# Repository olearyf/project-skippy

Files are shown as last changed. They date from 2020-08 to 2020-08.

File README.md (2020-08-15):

# project-skippy
**NOTE: this project is still underway!**

A cheap DIY rocket flight computer that tracks time from launch, pressure, altitude, temperature, acceleration.

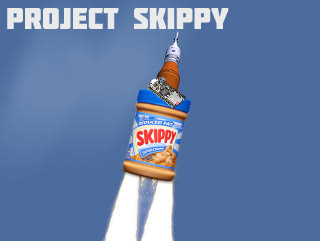
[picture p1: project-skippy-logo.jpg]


## About

While there are some neat physics tricks when it comes to approximating flight data for your model rockets, and while there are online weather apps and things to get such information such as local pressure and temperature, I thought it would be much more fun to get all this data myself. In addition to this, I can adjust the granularity to my preferences and make some sweet plots of some sweet data! Thus, Project Skippy is born; named because I started real work on the idea across from a jar of Skippy peanut butter while working in my kitchen. It's easy to use and implement, and in addition to this I supplied the 3D files for everything you need so you can print your own! All rockets use C Estes motors. 

Anyways, the idea is this: you print a rocket, make a flight computer, launch the rocket(with my super technical and complicated(jokes) remote ignition system), log the data during the flight, analyze it, and just have a good time. If that seems like something you're interested in, heres how:

## Parts List 💡
- [Adafruit Lithium Ion Polymer Battery - 3.7v 500mAh](https://www.adafruit.com/product/1578)
- [Adafruit Feather 32u4 Adalogger](https://www.adafruit.com/product/2795)
- [8 GB Micro SD Card](https://www.adafruit.com/product/1294)
- [MPL3115A2 - I2C Barometric Pressure/Altitude/Temperature Sensor](https://www.adafruit.com/product/1893)
- [Adafruit LIS3DH Triple-Axis Accelerometer](https://www.adafruit.com/product/2809)
- LED
- 220 ohm resistor (or whatever resistor you need to limit the appropriate current your LED can handle)
- some wires
- soldering iron (optional, depending on how you want to hook it up
- 3D printer (optional, you can strap this thing to any rocket your heart desires)
- M2 screws
- [small cheap camera](https://www.amazon.com/gp/product/B07X8LDZ9M/ref=ppx_yo_dt_b_asin_title_o07_s00?ie=UTF8&psc=1) (optional)

## Assembly (no BIC or TEQ 😉)
Below are some schematics made with Fritzing that detail how to wire it up. I recommend you visit the [tests](https://github.com/olearyf/project-skippy/blob/master/tests/about.md) folder and start with those, and then work your way up to the full code and full wiring below:

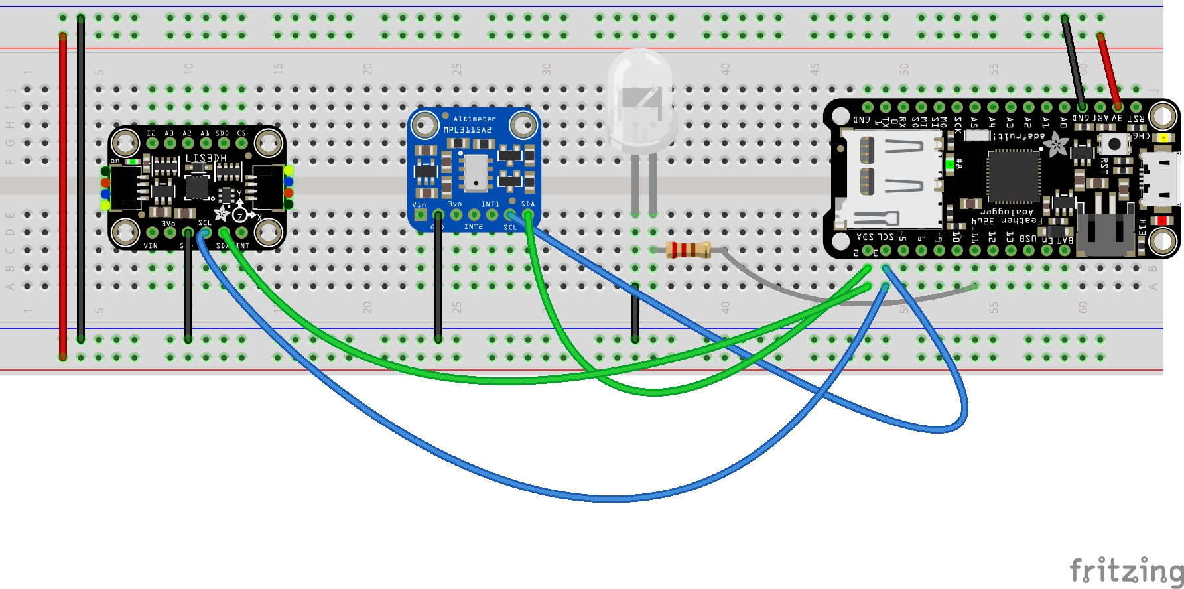
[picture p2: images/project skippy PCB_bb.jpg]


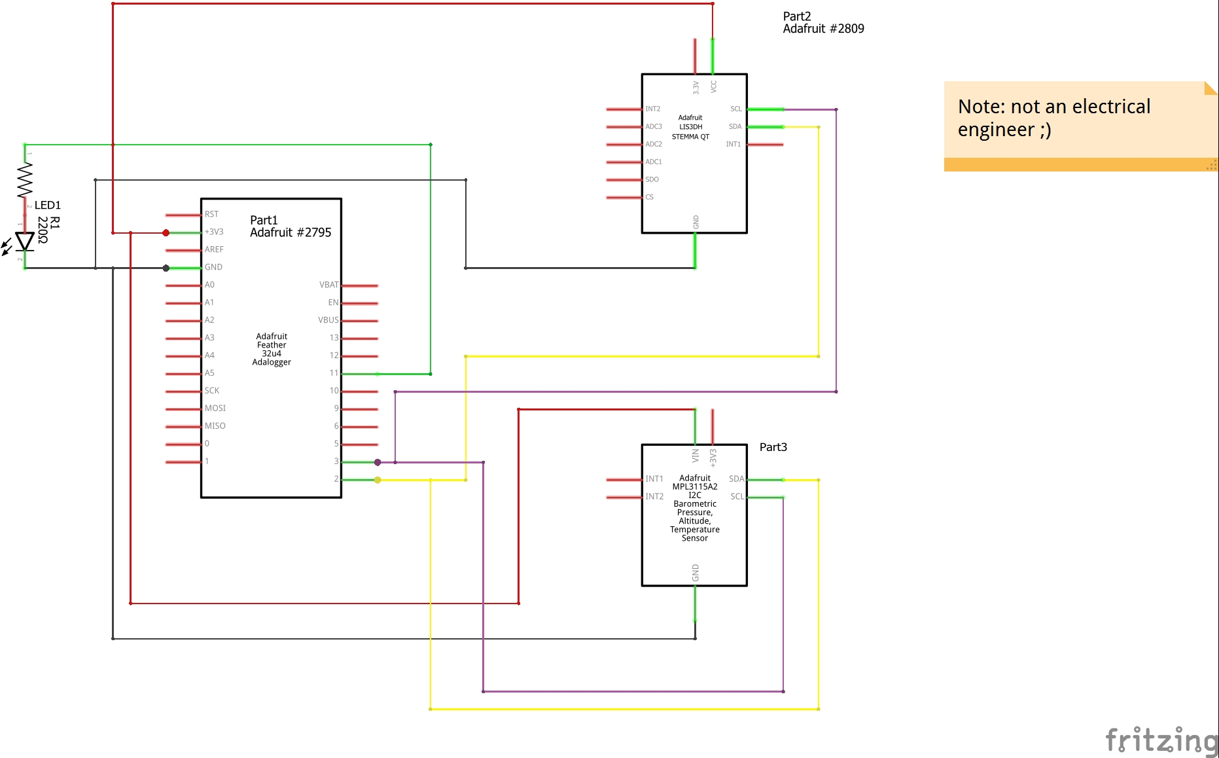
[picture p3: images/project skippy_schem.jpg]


Once it's all wired up you're ready to load the code!

Note: not shown in the schematic is the 3.7v 500mAh battery - I soldered a slide switch to break the positive terminal to act as a way to turn the computer on and off. Note, to initiate the program you may need to hit the reset button on the board.

Below is my set up while I was prototyping:

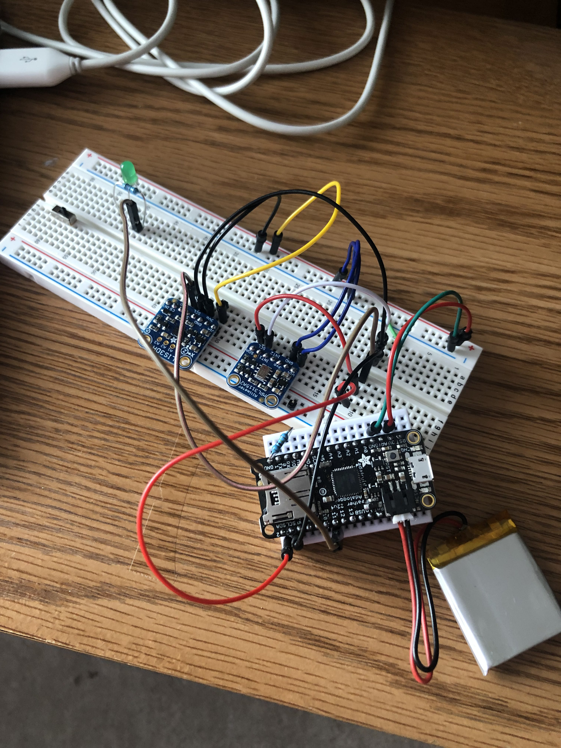
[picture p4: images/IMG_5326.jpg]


## Loading the Code 💻

To load the code, use the  [Arduino IDE](https://www.arduino.cc/en/main/software). Download [project-skippy-main.ino](https://github.com/olearyf/project-skippy/blob/master/project-skippy-main.ino) and open it in the IDE. From here, connect your Adalogger using a micro usb cable. Then, click upload. From the terminal, you should see it compile, and then flash the sketch to the board. If everything goes well, once it's done flashing you should see the LED turn on and log data for 10 minutes. If you encounter an error at compile time, it is most likely due to you either lacking the necessary libraries(defined at the top), or your board may possibly be connected to the wrong port. If it is the latter, try hitting the reset button after pressing upload, or restarting your computer.

## Attaching to Rocket 🚀

For my first launch I used an Estes C-11-0 rocket motor, since the camera and flight computer are fairly heavy. Below are pictures of the 3D files I made and printed that can be found [here](https://github.com/olearyf/project-skippy/tree/master/3D-files). They include a basic rocket body with a space for the motor, and a nose cone that fits via friction fit. The nose cone has a loop at the end that I recommend attaching a plastic bag streamer to, as when I launched it popped off and this addition helped slow its fall. If the motor is too loose for the base, wrap it in a layer of masking tape.

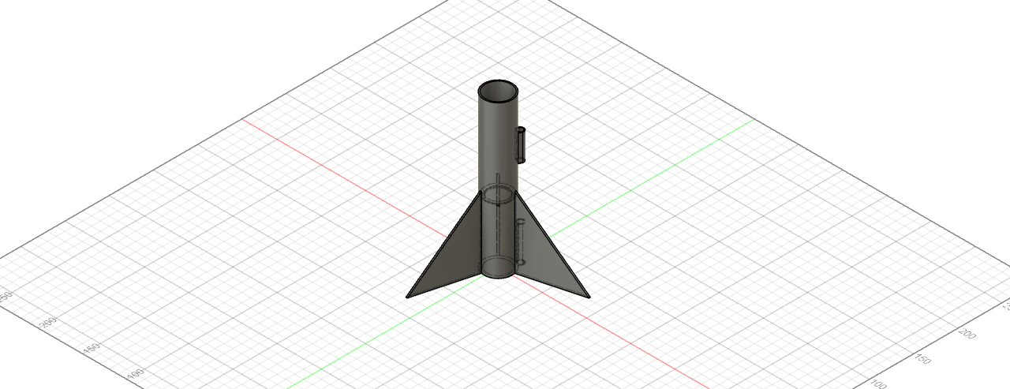
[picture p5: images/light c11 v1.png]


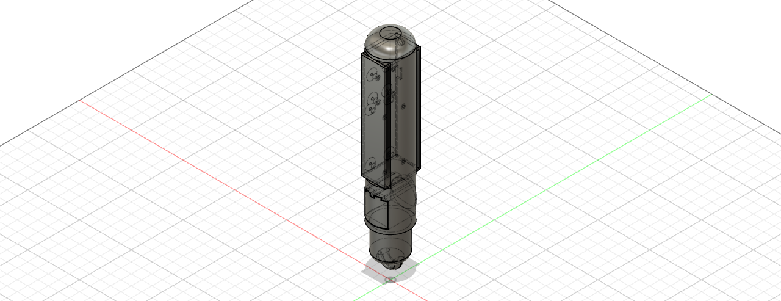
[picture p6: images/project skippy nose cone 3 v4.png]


Below is the finished rocket. You can see the LED and slide switch from the flight computer poking out, as well as the onboard camera. This one was named the EFun 3 X-PLORE because I launched it with one of my managers from my summer internship at Microsoft who came to Purdue and launched some rockets with me! (Skippy for scale).

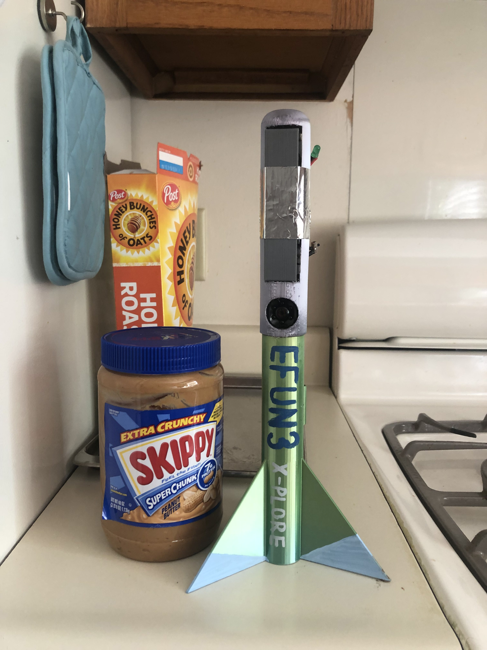
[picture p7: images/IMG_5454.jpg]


## Launch 💥

Unfortunately my camera was not recording the launch :(. However I'll launch again and upload a video soon! Data from the first launch with the rocket pictured above is found below.

## Analysis 📝

To use SkippyParser.py, install pandas and plotly using pip if you havent't already. Additionally, install Python if you need to. Then, from the command line, run the following:
```
python SkippyParser.py "path/to/your/flight/data/from/the/computer.csv"
```
This will parse your data and launch an html file that contains your data plots! Analyze to your heart's content; below is a readout from one of my launches:

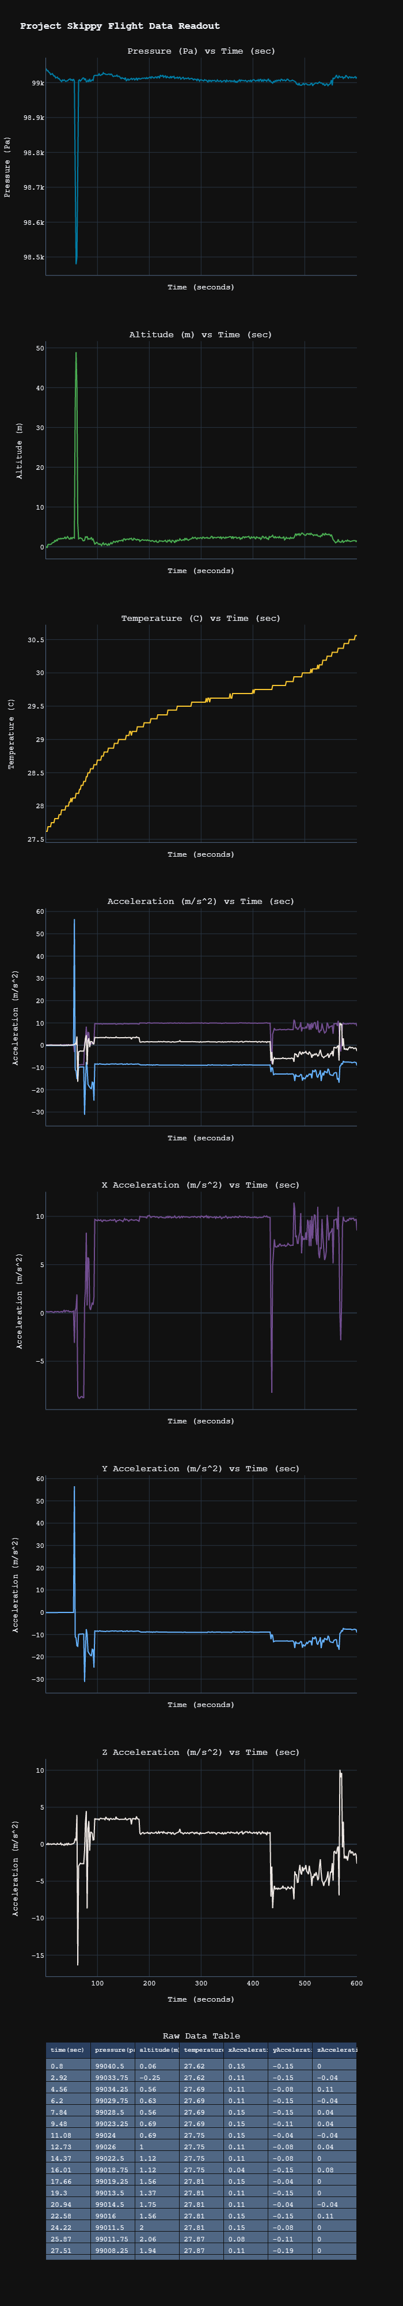
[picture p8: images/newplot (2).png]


While not the best data to recieve. . . it works! Now I just need to work on the items below to get my rocket to go higher. The full raw data can be found [here](https://github.com/olearyf/project-skippy/blob/master/data/FLIGHT32.CSV). Note that Project Skippy takes data for 10 minutes and a model rocket launch is usually far shorter than that ;).

## Things I'm Working On

- better housing! Right now it's all screwed into a box that gets taped in
- data filter
- better rocket design overall - I want to go higher!
  
### Important Notes (aka don't make the mistakes I did)

You may be wondering by some data values are read twice(such as temperature, pressure, and altitude). There isn't really any rhyme or reason to this; I just found that if I didn't do it I would get crazy values like <600 pascals. Reading it twice allows for some time for the sensor to really get the value(at least I think) so that's why it's in there.

UPDATE: I need to add a data filter! And I should be reading the values a lot more than just once.

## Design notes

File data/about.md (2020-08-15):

# Data

This is where I keep the data from launches!

### FLIGHT32.CSV

Flight data from a launch on 8/15/2020 using a C-11-0 motor.

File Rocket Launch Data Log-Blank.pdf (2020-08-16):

# Rocket Launch Data Log

## Launch Information

Date:

Location:

Approximate Time of Launch:

Reported Local Air Pressure:

Reported Local Wind Speed:

Reported Local Temperature:

Reported Local Elevation:

Description of Launch Conditions:

## Rocket Information

Rocket Name:

Rocket Height:

Largest Diameter:

Smallest Diameter:

Motor Type:

Camera?

Flight Computer?

Parachute?

Ignition Method:

Description of Rocket:

## Post Launch Information

Approximate Flight Time: | Maximum Height:

Description of Rocket Condition Post Launch:

Things that Went Right:

Things that Went Wrong:

Notes for Next Time:

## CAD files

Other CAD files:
3D-files/light c11 v1.f3d
3D-files/project skippy nose cone 3 v4.f3d

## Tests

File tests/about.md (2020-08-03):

# About
This folder, known as Tests houses all the test code I ran to devlope my flight computer, known as Project Skippy. Descriptions of each file are below, and comments within the code can further explain what is going on.
## adalogger-blink-test
This file is a sanity check for when you get your 32u4 Adalogger. It just makes the onboard LED blink. 
Note: no aditional wiring needed. Simply plug it in and upload your sketch.
## adalogger-sd-card-test
This file is a sanity check for writing to a micro sd card that is inserted into your 32u4. It writes some stuff to a .txt file on the sd card.
Note: no aditional wiring needed. Simply plug it in and upload your sketch.
## altimeter-test
This file is a sanity check for using your Adafruit MPL3115A2 pressure sensor. It is hooked up to the 32u4 using I2C(this sensor requires it), and this program prints out some basic stats.
Below is the wired setup and expected program output:

insert here!

## accelerometer-test
This file is a sanity check for using your Adafruit LIS3DH accelerometer with your 32u4 Adalogger using I2C(this sensor can also do SPI, which will be tested for the flight computer later on because it can transmit data at a faster rate). This program prints out some basic stats.
Below is the wired setup and expected program output:

insert here!

## combined-alt-accel-test
This file is a sanity check for using your Adafruit LIS3DH accelerometer and Adafruit MPL3115A2 altimeter on a single I2C bus on a 32u4 Adalogger. It logs basic data from both sensors at the same time.
Below is the wired setup and expected program output:

insert here!

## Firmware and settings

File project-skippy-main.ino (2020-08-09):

/*
 * Frances O'Leary 8/9/2020
 * 
 * This is code for project
 * skippy(V1), a homemade model rocket flight
 * computer. It logs data such as time since it
 * started logging, pressure, altitude, temperature, and xyz
 * accelertation in a csv file. It is intended to be used in conjunction
 * with SkippyParser.py, which plots the data.
 * 
 * Flow:
 *  - turn on device
 *  - if all goes well, green LED will turn on
 *  - device logs data for 10 minutes
 *  - logging stops (green LED off)
 *  - file closed
 *  - sketch terminates
 */

#include <SPI.h>
#include <SD.h>
#include <Wire.h>
#include <Adafruit_LIS3DH.h>
#include <Adafruit_Sensor.h>
#include <TinyWireM.h>
#include <USI_TWI_Master.h>
#include <Adafruit_MPL3115A2.h>

#define cardSelect 4
#define loggingLED 11
#define redLED 13


Adafruit_LIS3DH acceleromter = Adafruit_LIS3DH();
Adafruit_MPL3115A2 pressureSensor = Adafruit_MPL3115A2();
File logfile;
char filename[20];
float dataLoggingStartTime;
// data definitions
float time; // seconds
float pressure; // pascals
float altitude; // meters
float temperature; // degrees c
float xAcceleration; // m/s^2
float yAcceleration; // m/s^2
float zAcceleration; // m/s^2
float baseX; // to account for position of accelerometer
float baseY; // to account for position of accelerometer
float baseZ; //used to account for acceleration due to gravity

void setup() {
  
  // set pins
  delay(500);
  pinMode(redLED, OUTPUT);
  pinMode(loggingLED, OUTPUT);
  digitalWrite(loggingLED, LOW);
  digitalWrite(redLED, LOW);

  // see if card can be initialized
  if (!SD.begin(cardSelect)) {
    digitalWrite(redLED, HIGH);
    return;
  }

  // create filename that will not overwrite other flight data
  strcpy(filename, "/FLIGHT00.csv");
  for (uint8_t i = 0; i < 100; i++) {
    filename[7] = '0' + i/10;
    filename[8] = '0' + i%10;
    if (! SD.exists(filename)) {
      break;
    }
  }

  // attempt to open the file
  logfile = SD.open(filename, FILE_WRITE);
  if(!logfile) {
    digitalWrite(redLED, HIGH);
    return;
  }
  
  // write data schema on top line of file
  logfile.println("time(sec),pressure(pa),altitude(m),temperature(C),xAcceleration(m/s^2),yAcceleration(m/s^2),zAcceleration(m/s^2)");
  
  // attempt to connect to acceleromter at I2C address 0x18
  if (! acceleromter.begin(0x18)) { // if fails, try 0x19 as an alternative, or use address debugger
    digitalWrite(redLED, HIGH);
    return;
  }
  
  // options: 2, 4, 8, 16
  acceleromter.setRange(LIS3DH_RANGE_8_G);

  acceleromter.setDataRate(LIS3DH_DATARATE_50_HZ);

  // attempt to connect to pressure sensor
  if (!pressureSensor.begin()) {
    digitalWrite(redLED, HIGH);
    return;
  }

  // get base measurements
  sensors_event_t event;
  acceleromter.getEvent(&event);
  baseX = event.acceleration.x;
  baseY = event.acceleration.y;
  baseZ = event.acceleration.z;
  dataLoggingStartTime = millis();

  // set pins
  pinMode(redLED, OUTPUT);
  digitalWrite(loggingLED, LOW);

  // set LED to 'logging mode' (aka on)
  digitalWrite(loggingLED, HIGH);
}

void loop() {
  // get data
  time = (float)(millis() - dataLoggingStartTime) / 1000.0; // convert to seconds
  pressure = pressureSensor.getPressure();
  pressure = pressureSensor.getPressure();
  altitude = pressureSensor.getAltitude();
  altitude = pressureSensor.getAltitude();
  temperature = pressureSensor.getTemperature();
  temperature = pressureSensor.getTemperature();
  sensors_event_t event;
  acceleromter.getEvent(&event);
  xAcceleration = event.acceleration.x - baseX; // adjust for base measurements
  yAcceleration = event.acceleration.y - baseY; // adjust for base measurements
  zAcceleration = event.acceleration.z - baseZ; // adjust for base measurements

  // print data to file in predefined data schema
  logfile.print(time);
  logfile.print(",");
  logfile.print(pressure);
  logfile.print(",");
  logfile.print(altitude);
  logfile.print(",");
  logfile.print(temperature);
  logfile.print(",");
  logfile.print(xAcceleration);
  logfile.print(",");
  logfile.print(yAcceleration);
  logfile.print(",");
  logfile.print(zAcceleration);
  logfile.print('\n');
  if (time >= 600.0) {
    logfile.close();
    digitalWrite(loggingLED, LOW);
    return;
  }
  delay(100);
}

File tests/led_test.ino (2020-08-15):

/*
 * Frances O'Leary, 8/15/2020
 * 
 * This is a sanity check for when you've soldered
 * everything together and want to make sure the
 * basic connections work ;).
 * 
 */
void setup() {
  // put your setup code here, to run once:
  pinMode(11, OUTPUT);
  digitalWrite(11, HIGH);

}

void loop() {

}

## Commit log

2020-08-09 Project Skippy Main v1 final adjustments
    [project-skippy-main.ino]
2020-08-15 adding 3D files
    [light c11 v1.f3d, project skippy nose cone 3 v4.f3d]
2020-08-15 adding LED test
